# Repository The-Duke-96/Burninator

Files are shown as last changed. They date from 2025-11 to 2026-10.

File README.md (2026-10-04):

# Burninator v3.0 💪🐉🔥
This toolhead is yet another 4010 toolhead, heavily inspired by the [Dragonburner](https://github.com/chirpy2605/voron/tree/main/V0/Dragon_Burner) and the [A4T](https://github.com/Armchair-Heavy-Industries/A4T/tree/main), all props to them.  
Thanks to Reddit user pd1zzle for suggesting the toolhead name, I really took a liking to it.  
Thanks to Reddit user linuxgangster for suggesting, testing, and providing feedback for the MadMax toolchanger adaptation.  
Thanks to Reddit user Such_File_1825 for testing and providing feedback on the MGN7H carriage for V0
And thanks to anyone, who gave any suggestions, gave feedback, was sharing or contributing usermods.
 
<p>
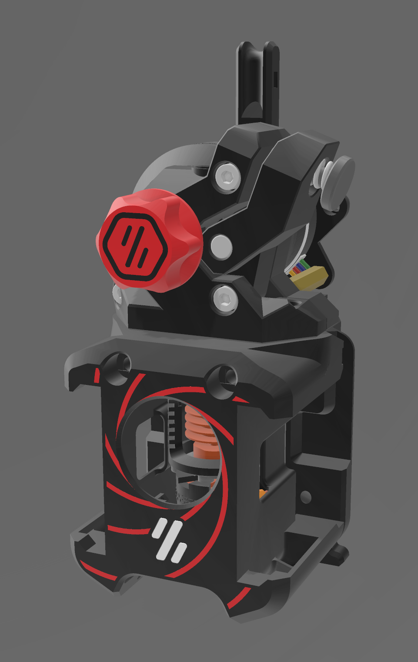
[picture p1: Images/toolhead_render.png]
 
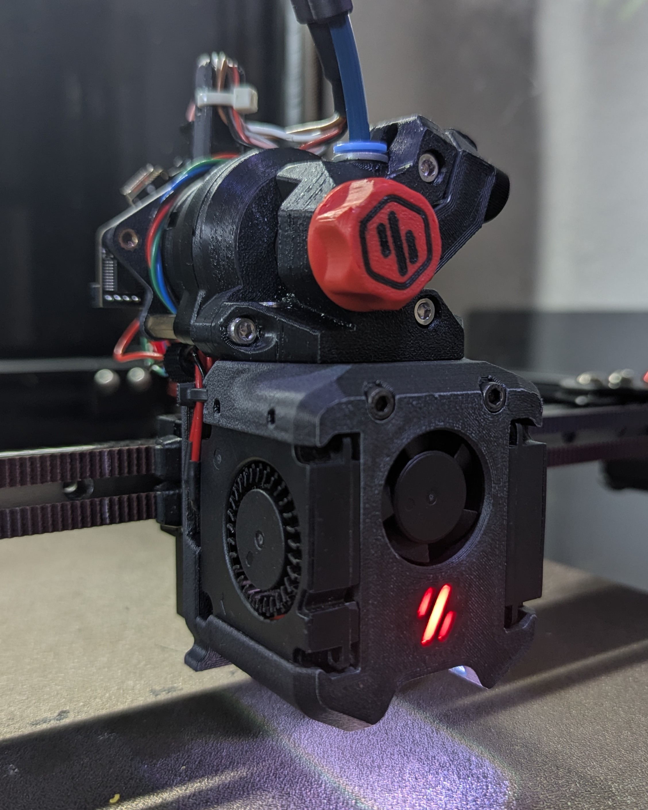
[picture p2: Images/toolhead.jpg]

</p>
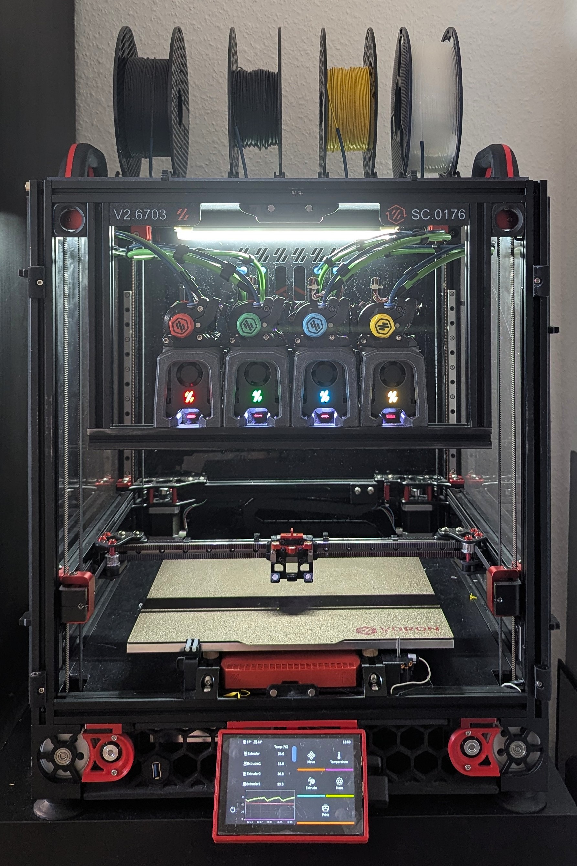
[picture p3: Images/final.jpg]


## But why?  
I created this toolhead because I wasn’t quite happy with the current toolhead options for my Stealthchanger.
After some testing, I decided to create my own toolhead to suit my use case and my printer.
I took features from the Dragonburner and the A4T and put them together, resulting in the Burninator.

## Features:
- Very small and compact, yet fits UHF hotends
- Monolithic cowl design
- Easy assembly and disassembly
- Stronger, 1.2 mm thick walls
- CFM optimized cooling and A4T's backflow inhibitors
- MGN12H, MGN9H, and MGN7H carriages compatible with up to 10 mm belts
- MGN12H and MGN9H carriages also compatible with the [Monolith_Gantry](https://github.com/Monolith3D/Monolith_Gantry) mod, as well as beacon,cartographer and klicky probe
- MGN12H also compatible with Tridex (6mm belts)
- StealthChanger ready
- MadMax ready

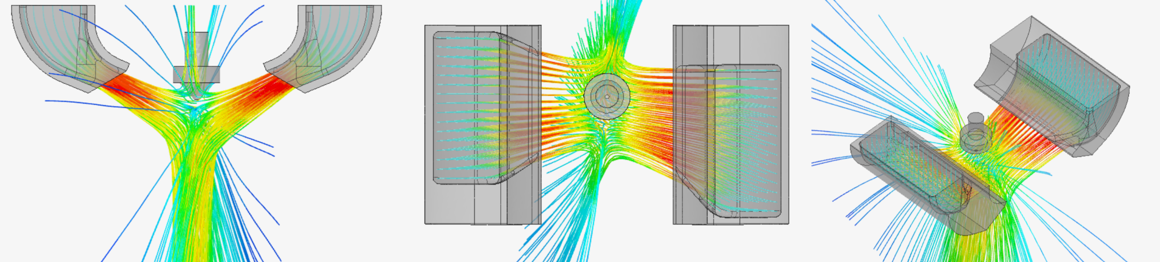
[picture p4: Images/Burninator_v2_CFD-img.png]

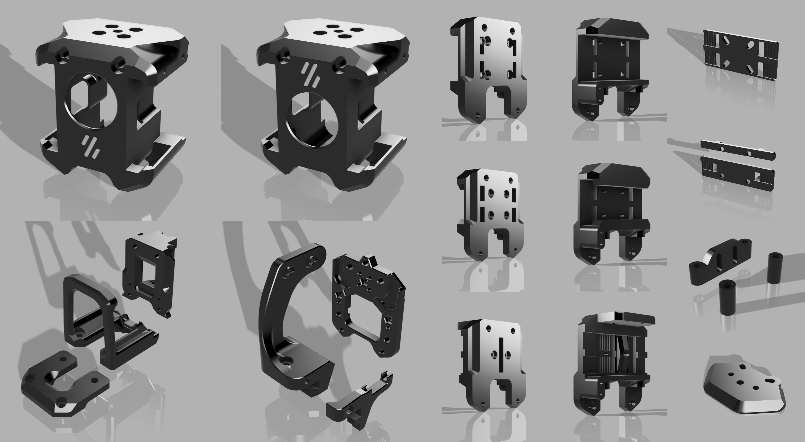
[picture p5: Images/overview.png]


## Compatibility:

**Hotends:** 
- Any top-mounted, Phaetus-style hotend
- SF: Dragon, NextG, TZ, etc.
- UHF: Dragon UHF, NextG UHF, Rapido HF, Dragon ACE (with spacer)
- Rapido UHF
- CHC-XL (+MZE)

**Extruders:**
- Orbiter / Galileo 2
- Sherpa Mini
- Sherpa Micro
- ECAS / Bowden
- LGX & LGX Lite (using the `LGX_adapter`)
- Or similar

**Note:**
- Using the custom parameters in Autodesk Fusion 360, you can adapt the design to almost any Phaetus-style, top-mounted hotend and extruder.

## What is planned?
Waiting for user feedback, opened issues, and suggestions or recommendations. I might also test out some ideas for potential future versions. Other than that, not much for now.  
Of course, CAD files are available for you to modify to your needs, and if you want, you can contribute is as a [Usermod](https://github.com/The-Duke-96/Burninator/tree/main/Usermods)
- looking into adding grove mount compatibility.

## How to Assemble?
Here's the [BOM](https://github.com/The-Duke-96/Burninator/blob/main/BOM.md).      
Here's a handy-dandy [Assembly manual](https://github.com/The-Duke-96/Burninator/blob/main/Assembly%20Manual.md).   

## Disclaimer:
- **Z-Axis Clearance:** If you use printed Z-joints, the toolhead's compact size might cause the Z-rail carriage to hit the frame before the nozzle touches the bed. Workaround: Add taller spacers under the print bed or use shorter Z-joints.  
- **StealthChanger Door Buffer:** If using a door buffer, the `DraftShift_dock_adapter` is required, otherwise the shuttle cannot reach the toolhead.  
- **Sensor Mounts:** Ensure the `beacon/cartographer_spacer`, or `klicky_mount` is scaled in the Z-axis to fit your specific setup.  
- **Beta Files:** Some files are untested by me. If anything does not fit or work as expected, please open an issue or let me know.
- **Macro Adjustments:** Stock StealthChanger pickup and dropoff paths work, but you might need slight adjustments for the nozzle to properly scrub the wiper.  

```
params_dropoff_path: [{'y': 25, 'z':6.5}, {'y': 5, 'z':6.5} , {'y':0, 'z':6.5, 'f':0.5}, {'y':0, 'z':0, 'f':0.5}, {'y':0, 'z':-10}]
params_pickup_path: [{'y':0, 'z':-10}, {'y':0, 'z':0, 'f':0.5, 'verify':1}, {'y':0, 'z':6.5, 'f':0.5}, {'y': 25, 'z':6.5}]
```

## Support:
<a href="https://ko-fi.com/theduke96">
  
</a>

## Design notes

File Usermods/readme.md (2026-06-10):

## Usermods

If you modified the Burninator and want to share it with others, feel free to contribute a user mod.

- Fork the repository.  
- Create a folder in `Burninator/Usermods` with a descriptive name.  
- Add your files and optionally include a README with instructions or further information.  
- Create a pull request.  

**Note:**  
The following usermods:  
- Tridex carriage (just a test)  
- StealthChanger dock for Rapido-UHF  
- StealthChanger dock for CHC-XL  
- MGN12H_invertable_belt_fixture for 9 mm belts  
- Cowl for CHC-XL + MZE  
have been removed from the usermods because they were provided by me and are now integrated into Burninator v3.0

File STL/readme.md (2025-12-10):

# STL Files

- v1 is the old / first uploaded version.
- v2 is the new and current version, featuring optimized ducts for improved part-cooling performance.  
**Note:** v1 and v2 are not fully compatible, due to changes in the duct geometry and screw-hole locations, the dock, its cosmetic, the backplate, and the carriages all had to be adjusted accordingly.
- All printed parts are already oriented correctly for printing.
- Required print supports are built in.
- Cosmetics and their corresponding parts must be printed together, just align them and decide if and how you want to color them.  
**Note:** Aligning the cosmetic to the cowl, either eyeball it or use the following reference offsets:  
UHF cowl on X0/Y0, cosmetic X-1,75/Y0.35  
SF cowl on X0/Y0, cosmetic X0/Y-2.03

- For the LED diffuser, it's recommended to print it in white or clear filament. You can also leave out the logo LED and print it in any color you want.

---

# Assembly Manual

- Start by installing the heat inserts: two in the bottom rear, two on top of the cowl, two at the top of either the StealthChanger backplate or the MGN12H / MGN7H carriage, two in the back of the EBB mount, one in the bottom of the dock, and two M5 inserts in the dock adapter.

<p>
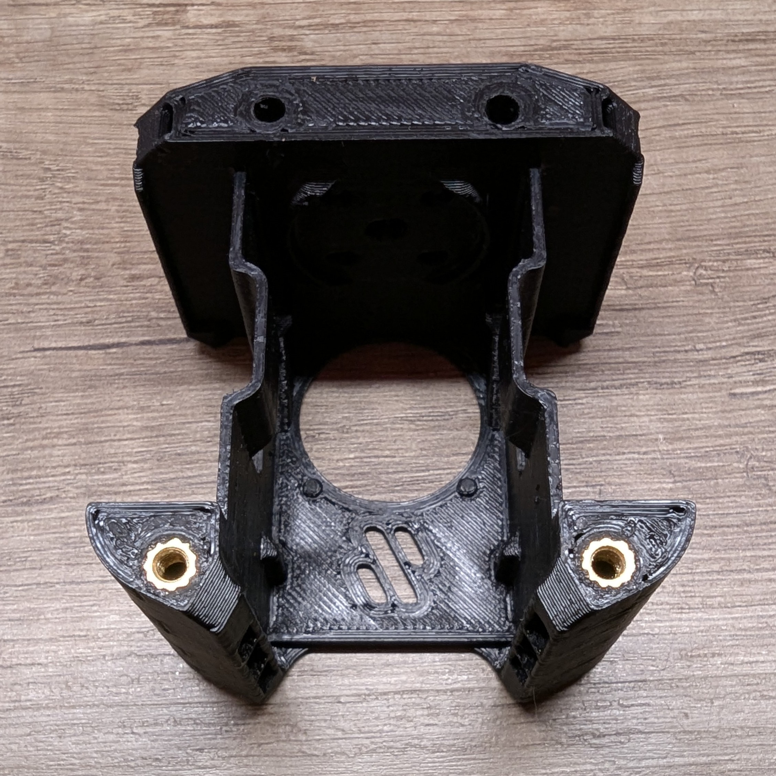
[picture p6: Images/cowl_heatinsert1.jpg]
 
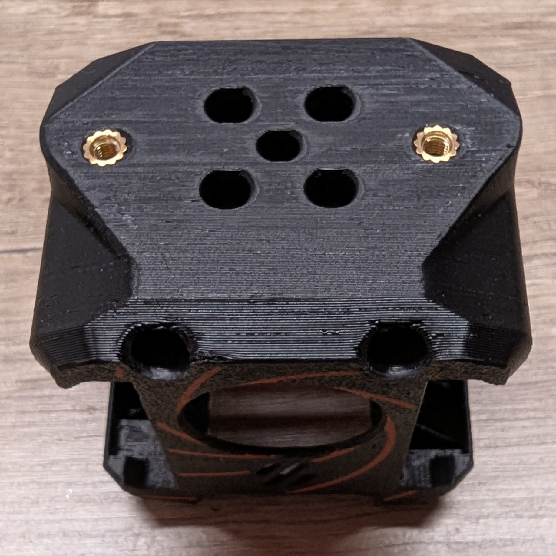
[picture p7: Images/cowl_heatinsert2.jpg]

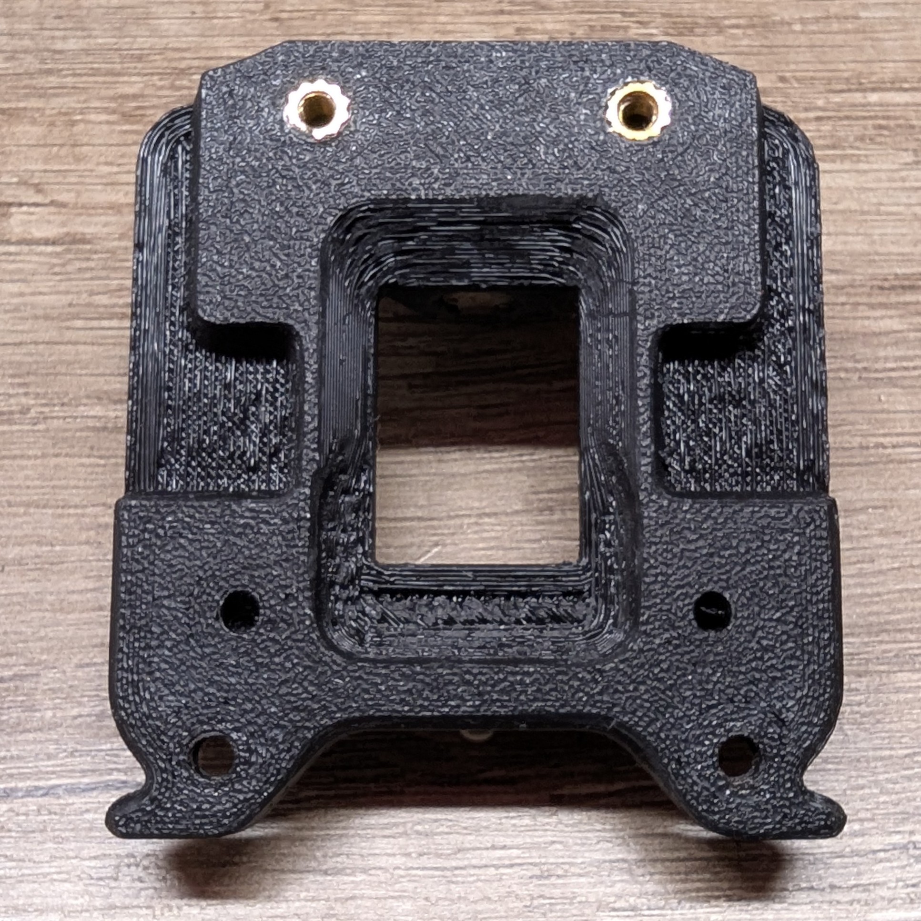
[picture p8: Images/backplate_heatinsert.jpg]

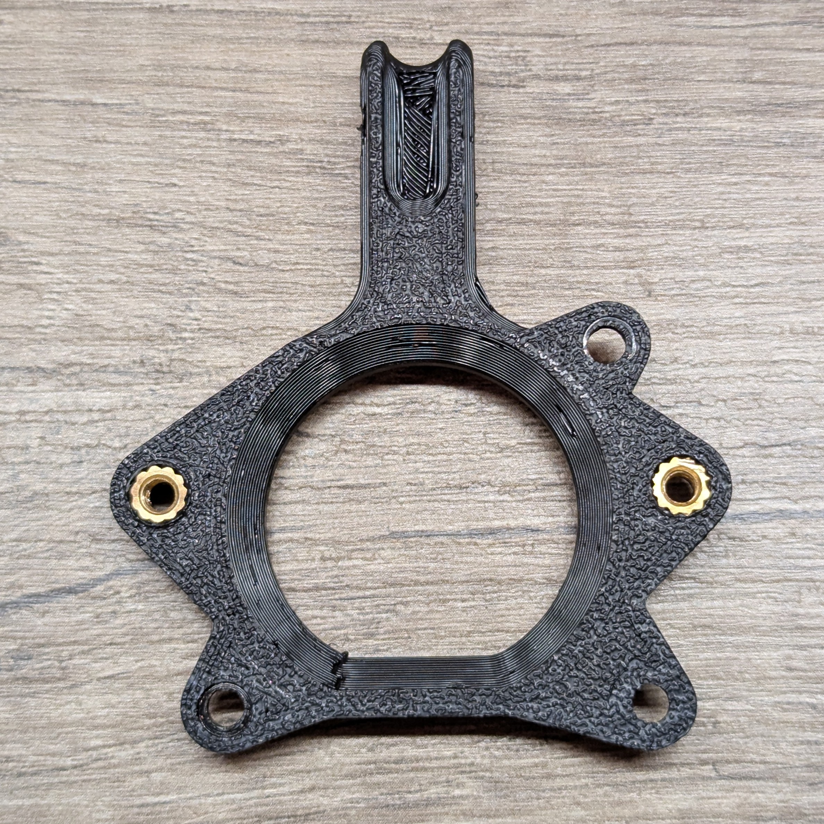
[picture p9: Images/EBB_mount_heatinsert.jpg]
 
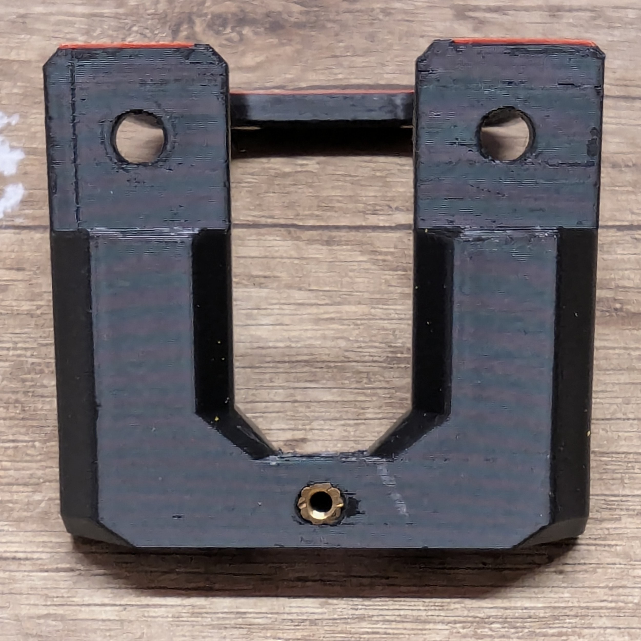
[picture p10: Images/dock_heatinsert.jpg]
 
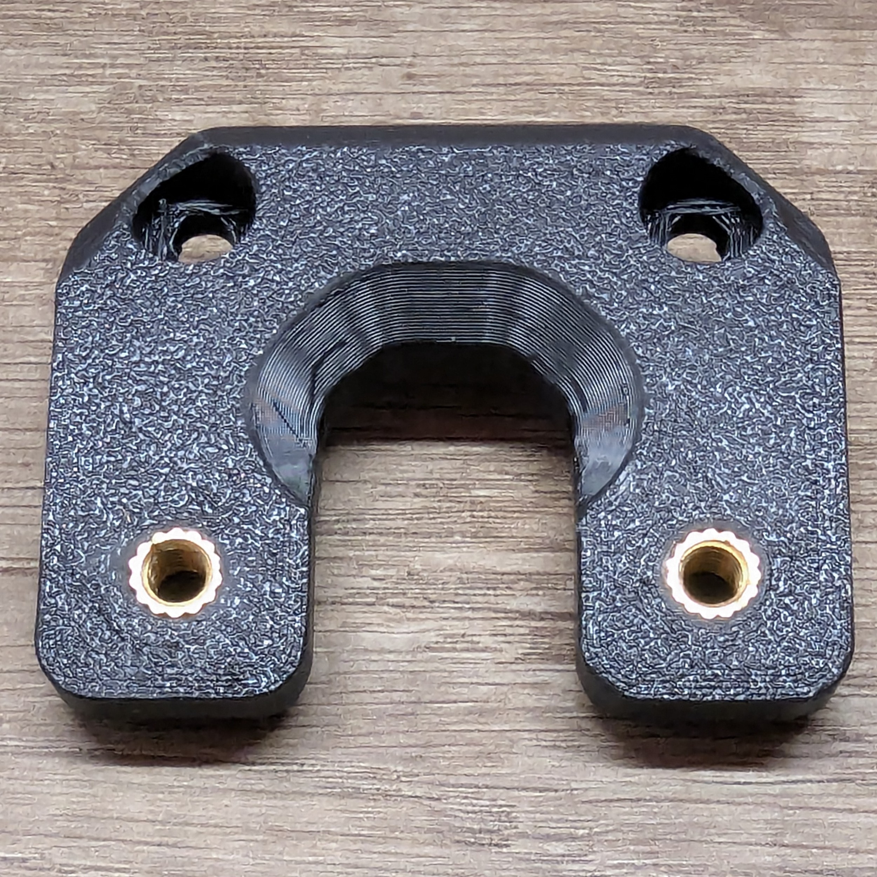
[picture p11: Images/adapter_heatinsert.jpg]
 
</p>

- Insert the 2510 fan from the back and slide it upward, wedging it into place. The two small nubs should fit into the bottom holes of the fan, securing it further. This works the same way as on the Dragonburner.
- Insert the LED diffuser into the Voron logo cutout.

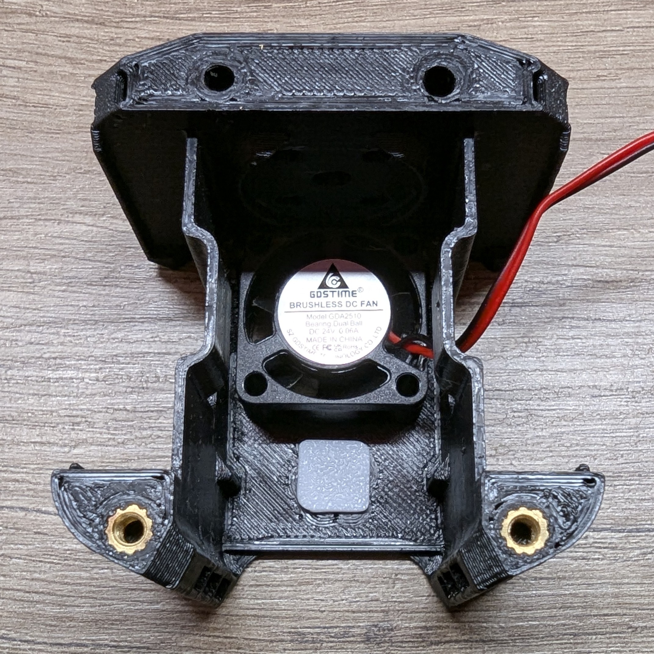
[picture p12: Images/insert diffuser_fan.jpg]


- Continue with soldering the LEDs. You'll need six pieces of 20mm wire and three pieces of 170mm wire.
- Solder the first three short wires to the OUT pads of the first LED.
- Solder the second LED, facing the opposite direction of the first.
- Solder the last three short wires to the second LED, facing the same direction as the first set.
- Solder the third LED so that it faces the same direction as the first LED and opposite the second.
- Solder the 170mm wire to the IN pads and crimp on the connector.  
  **Note:** Make sure the wires are soldered in the correct orientation as shown in the picture.
  
<p>
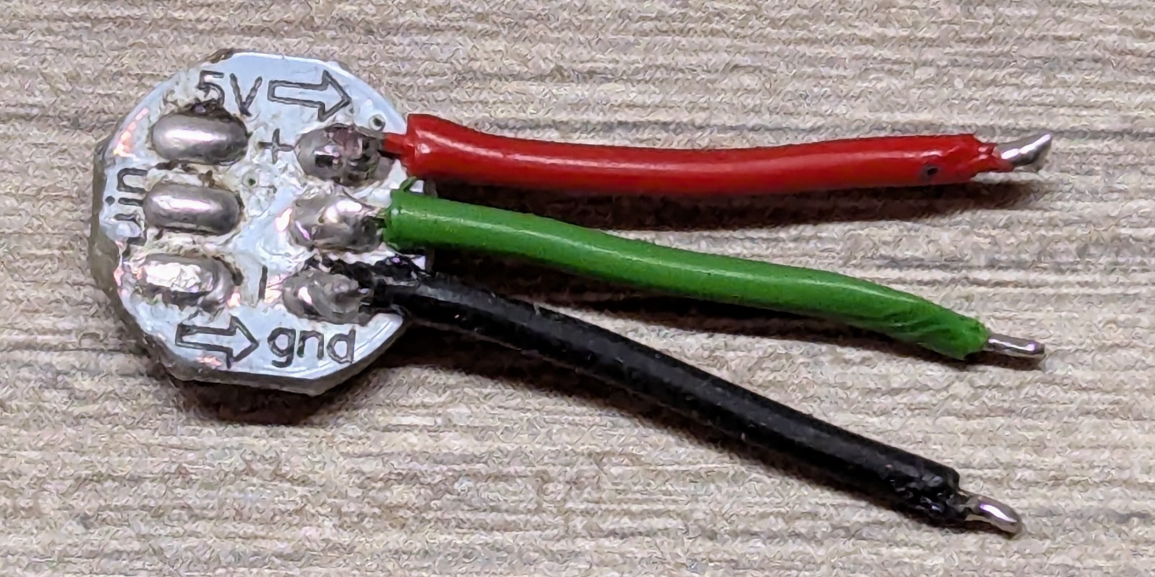
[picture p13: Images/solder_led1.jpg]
   
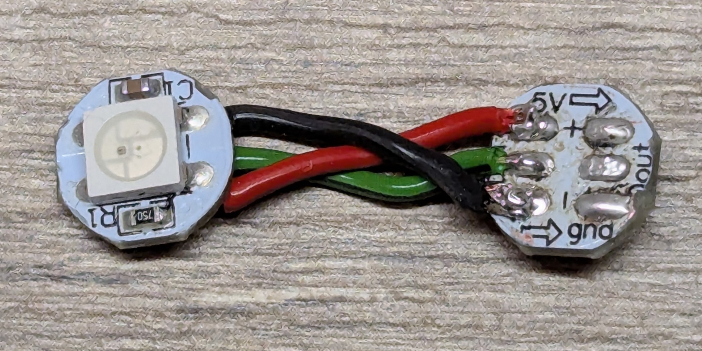
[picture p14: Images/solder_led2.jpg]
   
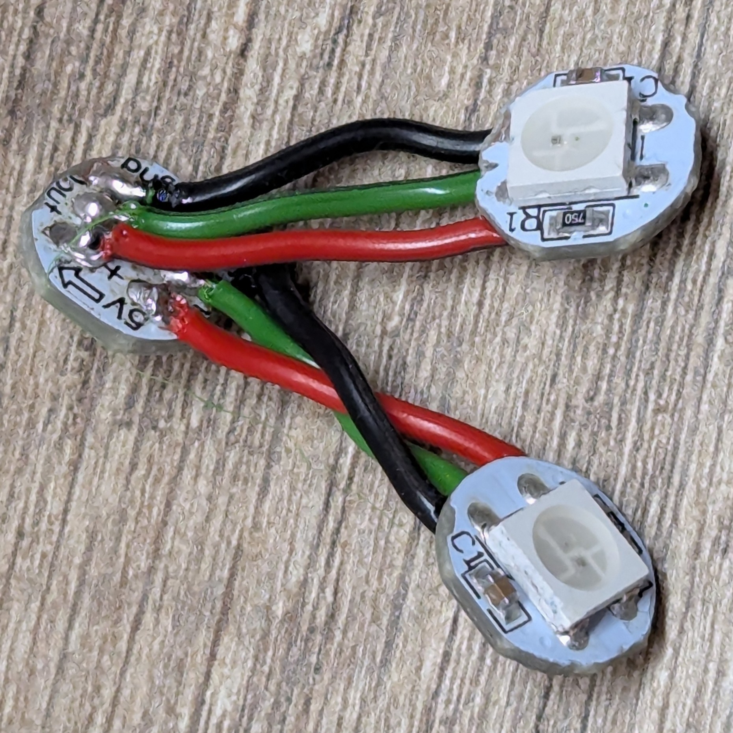
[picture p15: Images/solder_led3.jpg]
  
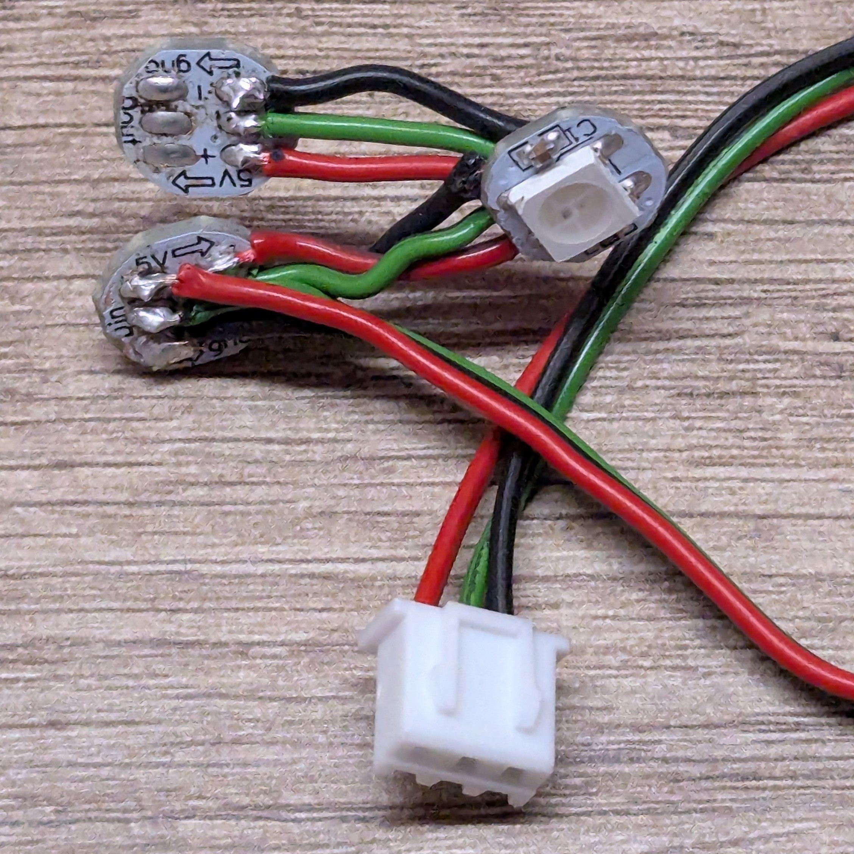
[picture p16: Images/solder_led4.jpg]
 
</p>

- Insert the second LED into the LED carrier first, then the remaining two, it’s easier that way.
- Insert the LED carrier from the back, placing the bottom edge into the cowl ledge. Tilt it, then press it firmly into place. Ensure the diffuser is seated in the front groove of the LED carrier.

<p>
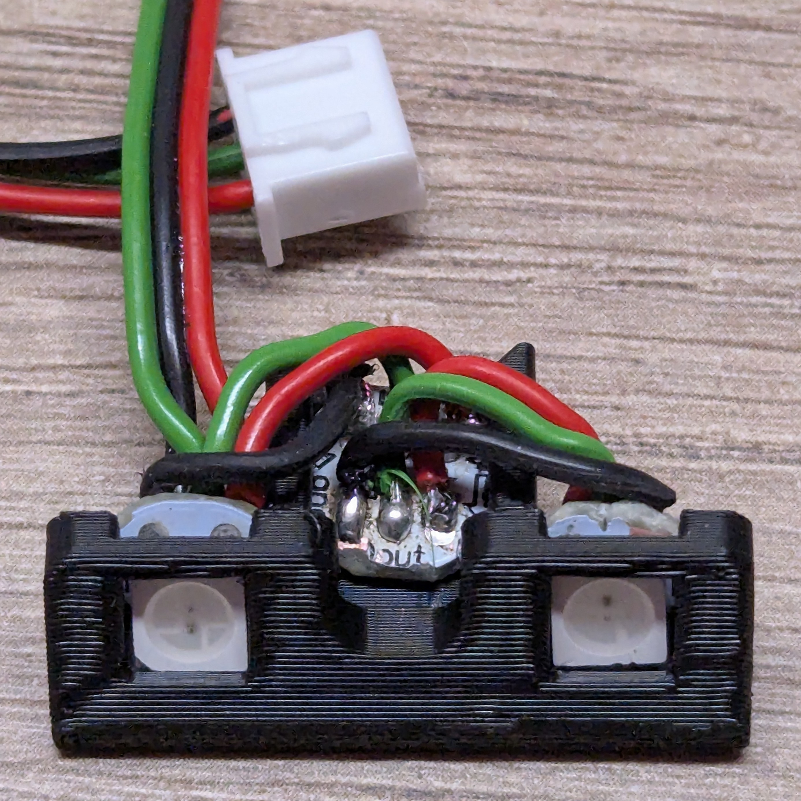
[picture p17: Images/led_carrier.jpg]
   
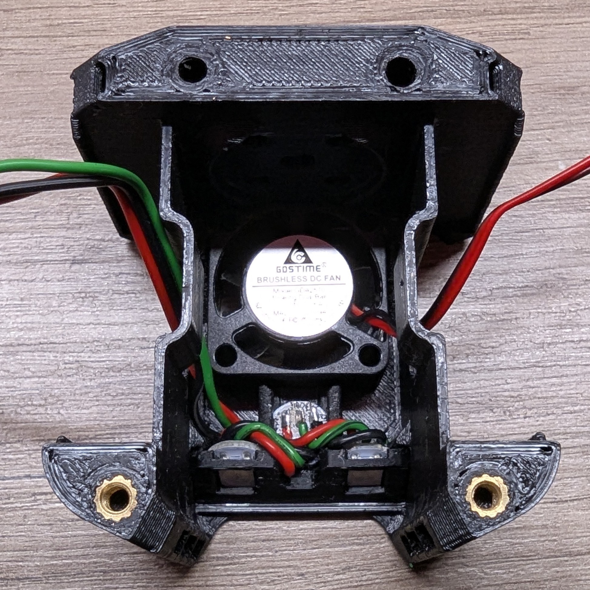
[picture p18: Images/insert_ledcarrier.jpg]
   
</p>

- For the 4010 fans: remove the front cover and glue in A4T’s Backflow Inhibitor (optional but recommended).  
  After the glue has dried, put the cover pack on.
- One of the fans needs its wires bent toward the back. You may also resolder the wires.
- Slide the fans into the sides of the cowl, same as on the Dragonburner.

<p>
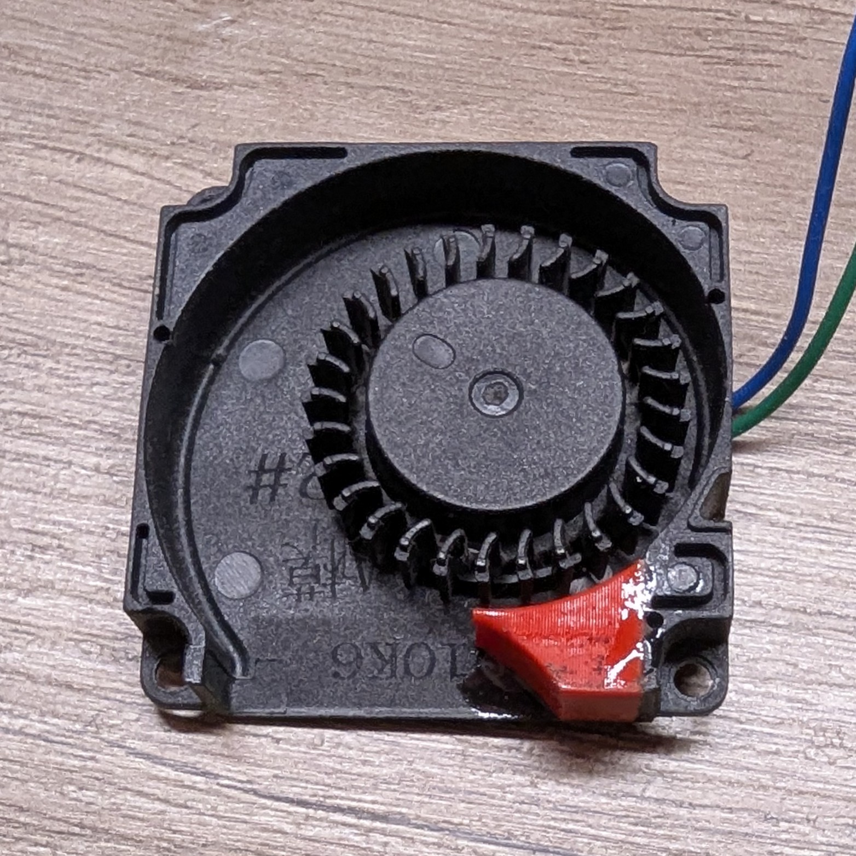
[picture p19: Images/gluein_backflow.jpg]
   
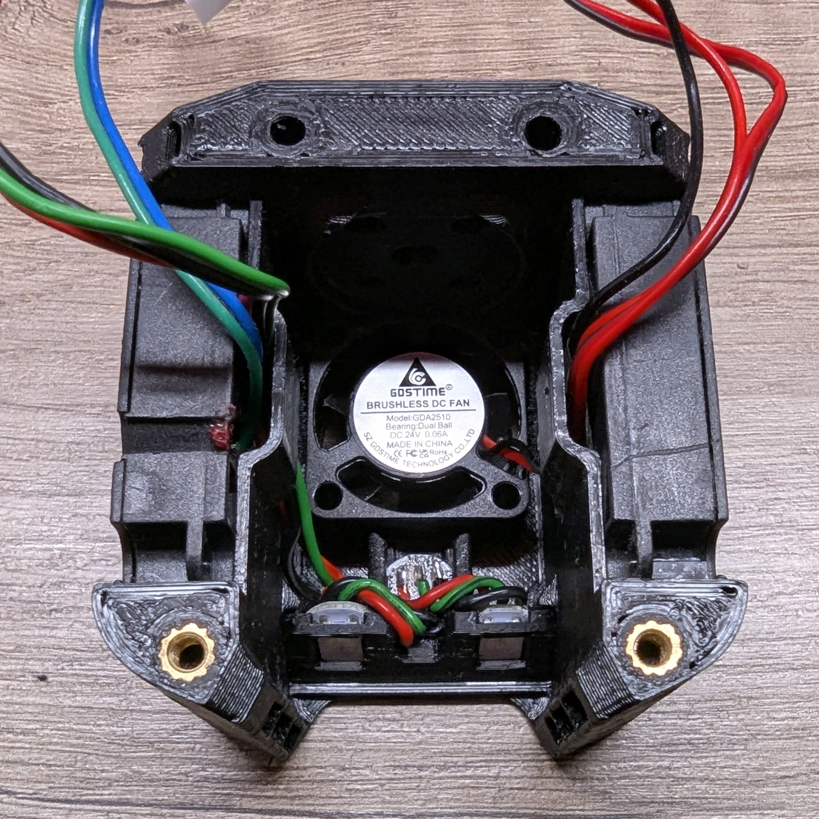
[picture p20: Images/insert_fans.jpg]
   
</p>

- Install the hotend. In my case, a Dropeffect NextG Fiber UHF is used. Ensure it's rotated correctly so the cables point toward the back corner.
- Route the thermistor wire with the cable sleeve to the opposite side, as it will not fit through the cowl and backplate cutouts. Route the heater wires on the other side, bending them so they will fit cleanly.

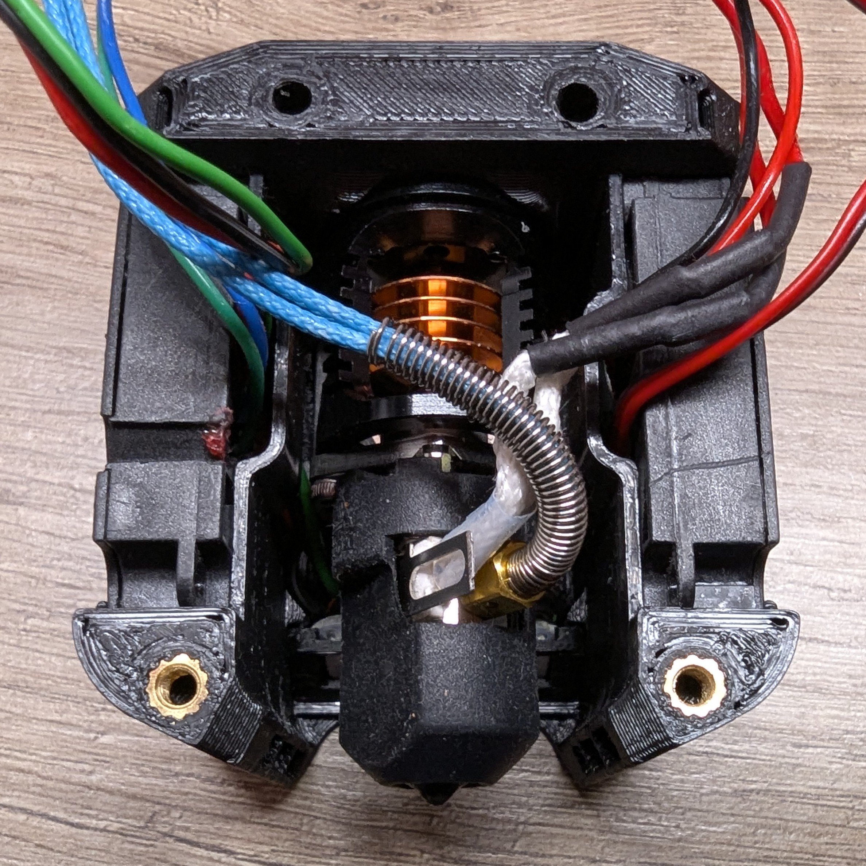
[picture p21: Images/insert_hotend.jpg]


- Place the backplate, wiggle the cables into position, and ensure the metal hose sits inside the backplate groove underneath the center hole. Screw it down.
- Install either M3x40 SHCS screws with a 3 mm spacer, or M3x35 SHCS screws without the spacer and place a 6×3 mm magnet on top.
- Route cables into the grooves and secure them with zip-ties.
- If using the StealthChanger backplate, install the OptoTap PCB.

<p>
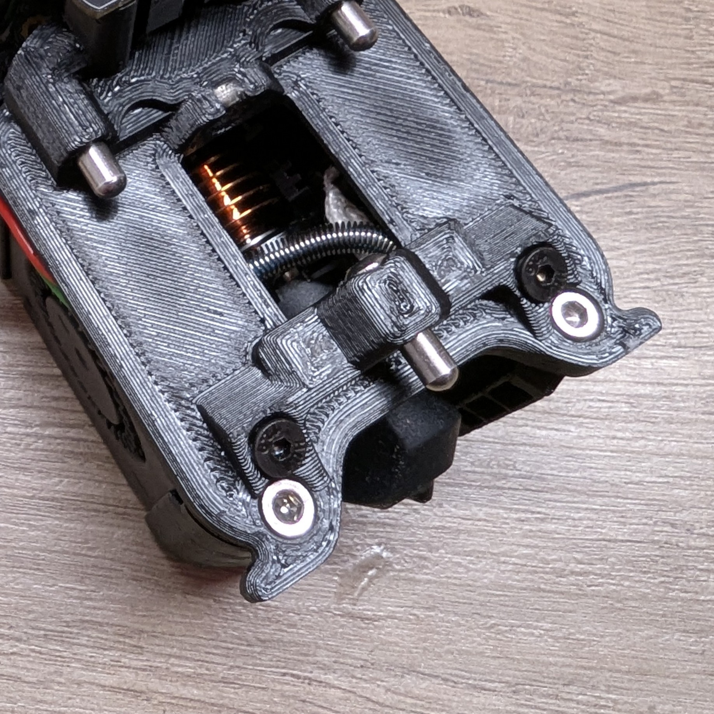
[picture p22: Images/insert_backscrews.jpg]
   
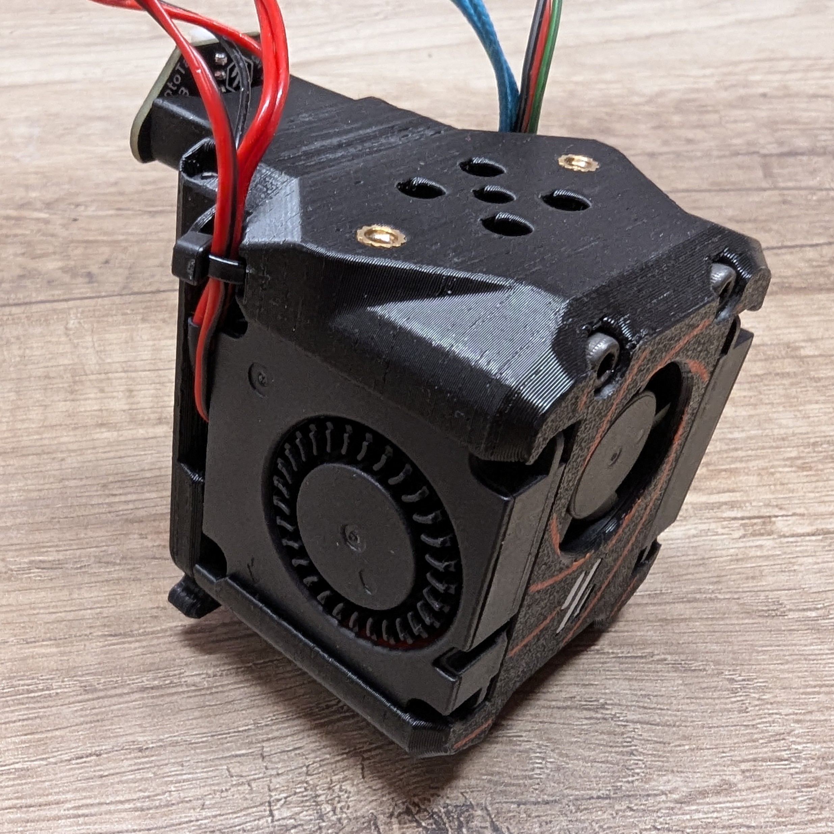
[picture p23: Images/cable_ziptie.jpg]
   
</p>

- Install a 22 mm PTFE tube and mount your extruder. In this example, the Galileo 2 WristWatch is used, followed by the toolhead PCB.
- In this setup, the EBB36_G2WW_Mount is required due to interference from the OptoTap.
- The toolhead is now complete.

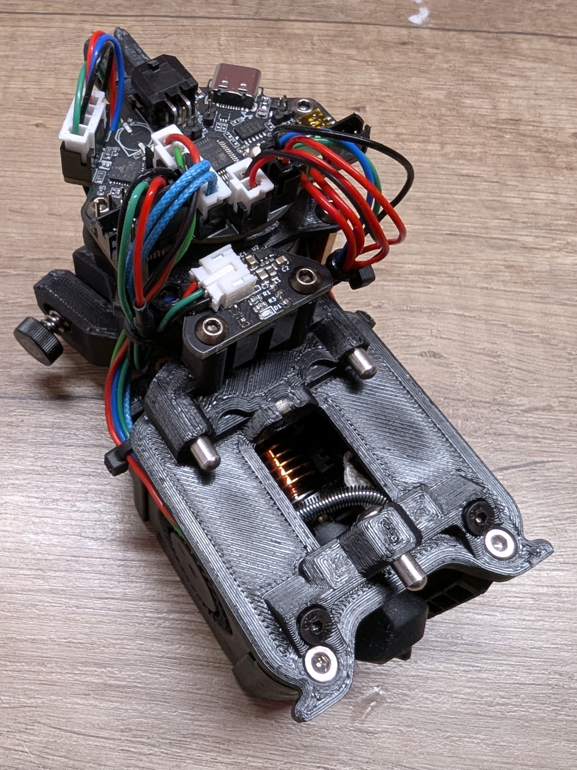
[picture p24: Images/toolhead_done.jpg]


---

# Cowl SF Assembly

- Assembling the SF cowl is only a little bit different from the UHF cowl.
- For soldering the LEDs, you need wires in the following lengths: 3 × 47 mm, 3 × 30 mm, and 3 × 170 mm.
- Start with the last LED and solder the 47 mm wires to the IN.
- Now solder the second LED, and then the first LED, using the 30 mm wires.
- Finally, solder the 170 mm wires and crimp on the connector.  
  **Note:** Make sure the wires are soldered in the correct orientation as shown in the picture.
- After that, place them into the LED carrier.

<p>
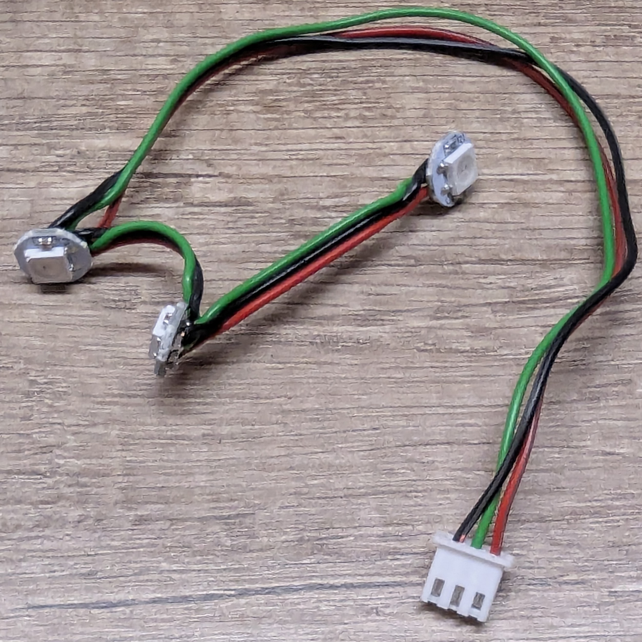
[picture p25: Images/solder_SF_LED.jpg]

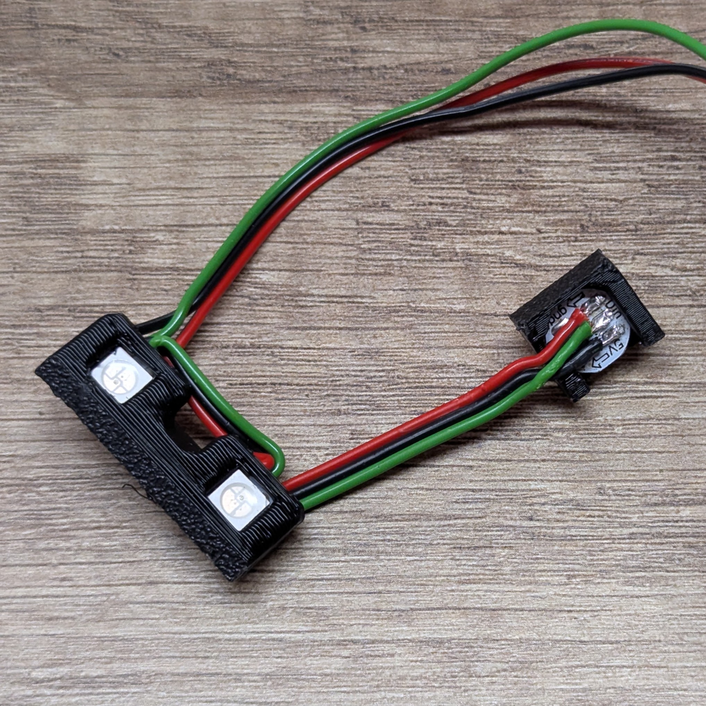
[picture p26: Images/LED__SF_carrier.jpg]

</p>

- Moving on to the cowl: first insert the LED diffuser and the top LED carrier. The cable should exit sideways into the cable channel.  
**Note:** Inside the cable channel are two little support ribs, as printing support. Just cut them away, 

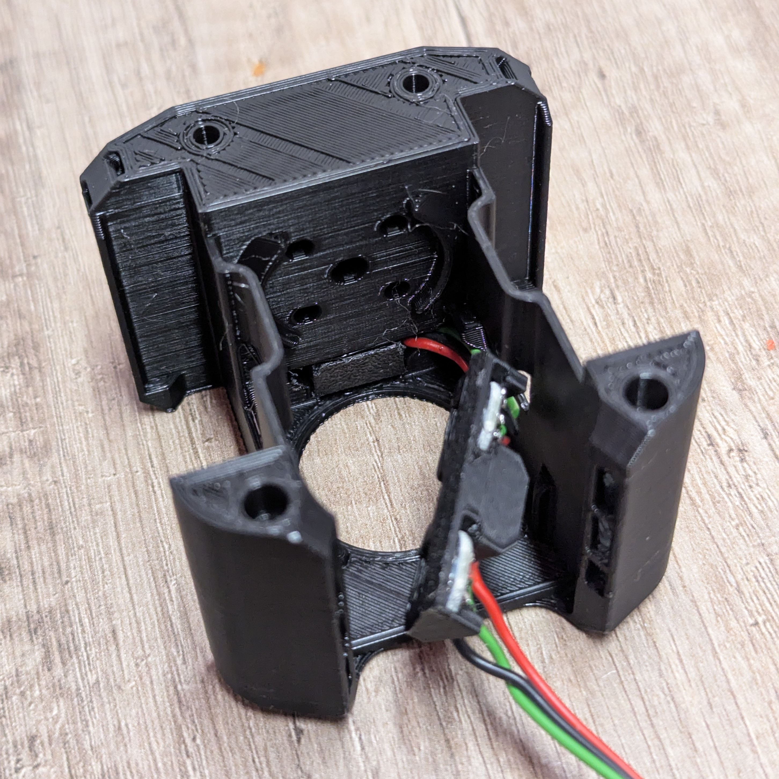
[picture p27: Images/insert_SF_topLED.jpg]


- Then tuck the cable into the corner and run it down along the wall. Push the larger LED carrier aside and insert the 2510 fan.
- After that, push the larger LED carrier into place.  
  **Note:** Due to the tight space, routing the cable and seating everything can be a bit tricky. The better the soldering job and the thinner the wires, the easier it gets.

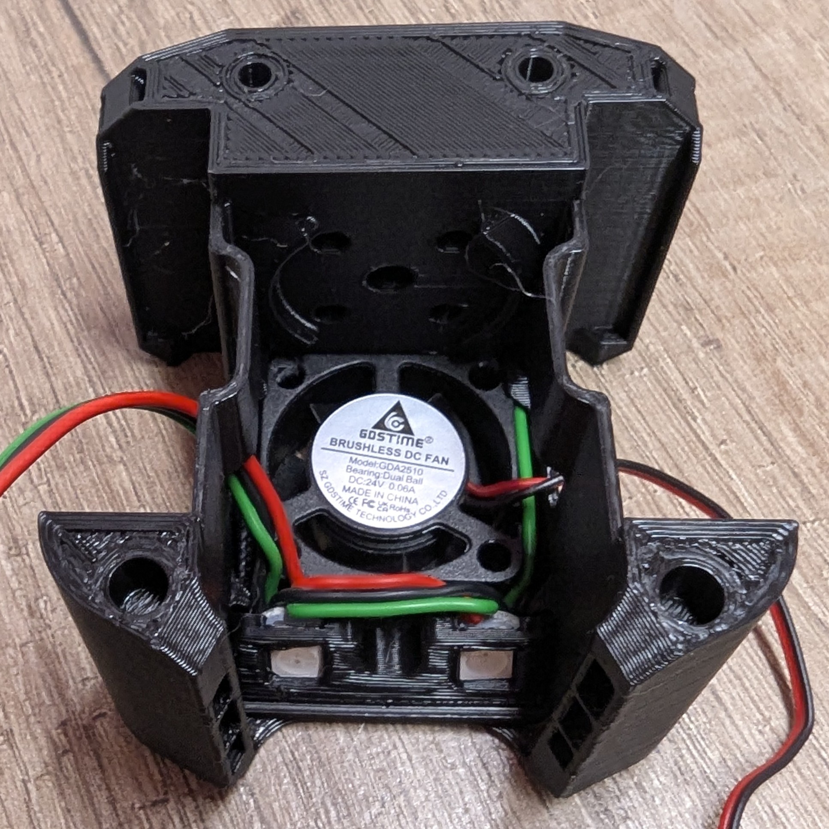
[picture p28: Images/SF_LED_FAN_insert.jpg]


---

# Dock Assembly

- Insert the 31 mm spring steel blocker into the rear slit and secure it with an M3x5 screw.
- Take a 23 mm PTFE tube for the wiper, bend it in the middle, wedge it into the back holder, then press down to straighten it out.
- Press the magnets into the top.
- Mount the dock onto the crossbar, optionally using the adapter.

<p>
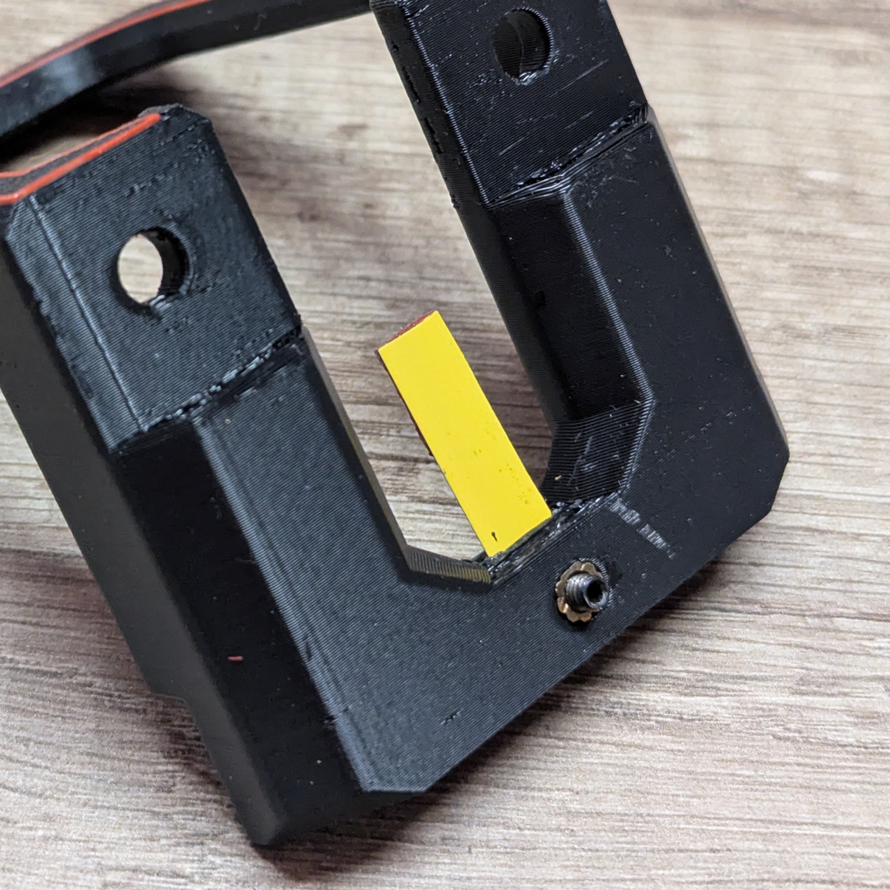
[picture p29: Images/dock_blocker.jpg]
   
   
</p>

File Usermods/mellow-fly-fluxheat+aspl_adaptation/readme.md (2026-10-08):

# Mellow Fly Fluxheat with ASPL level sensor adaptation
UHF cowl and MGN12/9/7H Backplate adjusted for the Mellow Fly Fluxheat with ASPL level sensor, using the CAD parameters as well as a shim to mount the aspl pcb between the EBB36 mount and EBB36 pcb.
As by userrequest, I have added it here as a usermod.

## fly-aspl_adapter.stl


**note:**
- Put a M3 heat insert into the center hole.
- A litte bit of support is needed.
- don't  forget the appropriate belt clampage parts 
- Using the fly-aspl_adapter, will extend the toolhead into the back by 8mm! Connectors on the side should be still accessable.  

## fly-aspl_adapter_v2.stl


**note:**
- Put a M3 heat insert into the center hole.
- no support needed
- put this behind the EBB36_mount
- use sufficiently long standoffs

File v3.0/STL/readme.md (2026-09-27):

# STL Files

- Objects are not oriented correctly and do not have built-in support structures. Keep this in mind when slicing, using manuall support just on the critical faces is recommended.
- Print the `LED_diffuser`, and optionally the `LED_carriage`, in white for better light distribution.
- Scale `klicky_mount` and `beacon_cartographer_spacer` in Z to your needs.
- Print settings: Follow the Voron Design advice [here](https://docs.vorondesign.com/sourcing.html)

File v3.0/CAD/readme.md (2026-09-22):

# CAD Files

- Use these files if you wish to modify something.  
- Keep in mind that the fan duct must blow air to the correct area: the tip of the hotend nozzle should sit about 2 mm beneath the lowest part of the cowl.  
- `backplate_base`, `SC_shuttle_base` and `MGNxH_carriage` are base bodies you can use to build upon.
- Extruder mounting holes and the ECAS adapter are present as a negative bodies that needs to be cut out.  
- I made use of custom parameters you can use to adapt the toolhead to almost any hotend:  
  - `hotend_length`: Lengthens the cowl to your hotend size.
  - `hotend_screwhole_radius`: Adjusts the hotend mounting holes.
  - `DS_adapter_length`: Shortens or lengthens the adapter to fit your existing DraftShift docks.
  - `extruder_screwholes_left`: Adjusts the center distance for the left extruder mounting hole.
  - `extruder_screwholes_right`: Adjusts the center distance for the right extruder mounting hole.
  - `heat_insert_diameter`: Adjusting the hole size for the M3 heated inserts.
- I also provided a convenient Python export script that I use. It changes the parameters, makes the cuts, and exports all the files.  

**Note:** 
The Python script was written with the help of AI. 
I'm way too stupid to do it myself, so I claim no credit for it. 
All credit goes to those, which training data were used.

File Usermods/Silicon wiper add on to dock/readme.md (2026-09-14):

Direct replacement of PTFE tubing wiper in favor of a silicone wiper. 

This is designed to be a bit tight of a fit into the existing PTFE slot. No modifications to the dock itself but you have have to snap them into place. The wiper used [is these that are common on the A1 printers](https://a.co/d/09I6NoFP) so they are available from all over the place. They are trimmed down to about 4 rows and slide into place from one side. The ones i had have some glue on the bottom with a peel off strip to expose it. I would imagine most do but a drop of glue would work too if needed. 

The print should be with the Nozzle wiper portion facing up. Some support of whatever flavor you like on the bottom, it's a super fast print so it's easy enough to do some testing with what works for your setup.

When installing put the short overhang side out toward the shuttle and the 45 degree slash in toward the dock body. If you insert backwards the pin slots on the dock will catch when grabbing/dropping off and make less than ideal noises. 

<p align="center">
  Dock wiper
</p>

<p align="center">
  Front View
  Back View

The original docking params may need to be adjusted for the wiper similar to the adjustments made for the PTFE tube version in the main repo. 

The magic values to get a little wipe on the way in and on the way out is the First 2 on Z on drop off and the last Z on pickup. If those number are different you get a little bit of a ramp, i have them at the same level right now so it wipes across the wiper just enough to pass through but now so low as to try to pull the wiper from the cradle. It's certain a little balance but it's not hard to find. 

I changed them both from 4 to 2 (based on the original Easy-tool-changer repo numbers) so it wipes directly across the silicone pad instead of coming up high just across the top of the wiper. 

```
params_dropoff_path: [{'y':9.5 ,'z':2}, {'y':9.5, 'z':2}, {'y':5.5, 'z':0}, {'z':0, 'y':0, 'f':0.5}, {'z':-10, 'y':0}, {'z':-10, 'y':16}]
params_pickup_path: [{'z':-10, 'y':16}, {'z':-10, 'y':0}, {'z':0, 'y':0, 'f':0.5, 'verify':1}, {'y':5.5, 'z':0}, {'y':9.5, 'z':2}, {'y':9.5 ,'z':2}]
```

In order to tune this the Dock_Tuner Macros work great to come at them slowly and test your height requirements with minimal carnage.

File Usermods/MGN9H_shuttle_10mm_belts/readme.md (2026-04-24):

# Shuttle for MGN9H shuttle with 10mm belts
This is a modified StealthChanger shuttle for the MGN9H and 10 mm belts, it uses the shuttle keeper modified as well for MGN9H and 10 mm belts.
Use this and proceed as shown in the StealthChanger documentation.

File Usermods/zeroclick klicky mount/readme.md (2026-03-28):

# Zeroclick Klicky Mount
A simple mod of the zeroclick probe to mount it like the klicky probe

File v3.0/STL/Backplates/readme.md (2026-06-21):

# Backplates
**note:**
Use the _alt (alternative) belt_clamp_plates, if you have trouble with the belts. Those are thicker and allows the belt be loop and clamp from both sides, but it also adds 1.4mm in Y.

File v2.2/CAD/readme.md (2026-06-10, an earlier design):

# CAD .step file

- Use these files if you wish to modify something. 
- “Burninator_RAW.step” offers a clean base version of the Burninator, with no cosmetics, no spiral pattern, no extruder mounts, and no front LED logo, so you can use it as a foundation to build on.
- Keep in mind that the fan duct must blow air to the correct area: the tip of the hotend nozzle should sit about 1.5 mm beneath the lowest part of the cowl.
- The CAD files do not include the subtraction for the MadMax screw holes on the cowls, in order to keep the file size down.
The component called “cowl_screwhole_extensions” in Burninator, MadMax is exactly what it says. Combine it with any cowl of your choice, do the screw hole subtraction, and you are done.

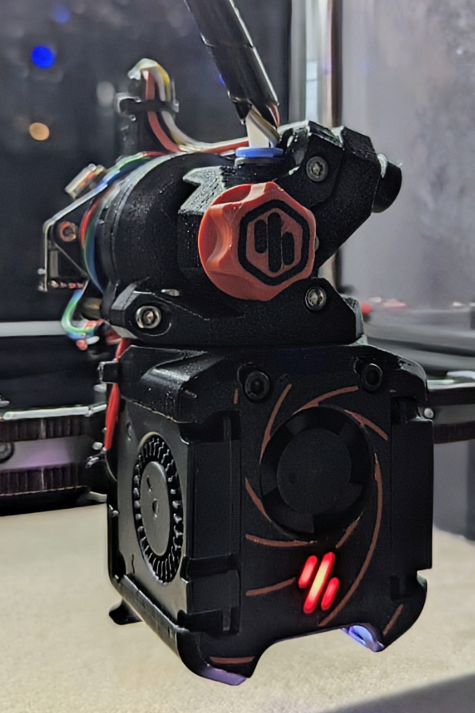
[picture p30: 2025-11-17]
Images/Toolhead.jpg

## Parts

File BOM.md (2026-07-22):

# BOM — Burninator v3.0

## Cowl
- 4x    M3x4mm heat inserts
- 2x    M3x40mm SHCS magnetic 
- 2x    M3x6mm BHCS
- 1x    2510 fan (Delta ASB02505SHA-AY6B or similar high cfm fan recommendet)
- 2x    4010 blower fans
- 1x    LED_diffuser
- 1x    LED_carriage
- 3x    PCB-LEDs (neopixel)
- 1x    hotend
- 4x    M2.5x6-8mm hotend screws (torx BHCS recommended)
- 1x    ptfe tube (short, between hotend and extruder)
- 2x    2,5mm cable zip tie

## MGN12H_ and MGN9H_carriages
- 4x    M3x4mm heat inserts
- 1x    belt_clamp_plate / tridex_clamp_plate(+_opp)  
- 4x    M3x6-8mm SHCS    

## MGN7H_carriage
- 6x    M3x4mm heat inserts
- 1x    belt_clamp_plate / tridex_clamp_plate(+_opp)  
- 4x    M2x4-6mm SHCS   
- 2x    M3x6-8mm SHCS
- 2x    MGN7H_belt_clamp_[2x] 

## klicky_mount and beacon_cartographer_spacer
- 2x M3x(length depending) SHCS

## lgx_adapter
- 4x    SHCS extruder screws
- 2x    M3x6mm SHCS

## SC_backplate
- 2x    M3x4mm heat inserts
- 3x    4x12mm dovel pins
- 5x    M3x8mm BHCS
- 1x    6x3mm N52 magnet
- 2x    M3x6mm FHCS
- 1x    OptoTap PCB sensor

## SC_dock_back
- 1x    M3x4mm heat inserts
- 2x    M3x6-8mm SHCS
- 1x    M3x4mm SHCS (grub screw recommended) 
- 1x    10x28mm spring steel blocker
- 1x    4x19mm ptfe tube

## SC_dock
- 2x    M3x4mm heat inserts
- 2x    6x3mm N52 magnet    
- 2x    M5x10mm BHCS

## SC_adapter
- 2x    M5x8-10mm heat inserts
- 2x    M5x10mm BHCS

## SC_MGN12H_ and _MGN9H_shuttles
- 2x    M3x4mm heat inserts
- 1x    belt_clamp_plate 
- 3x    4x6x6mm bushing
- 3x    6x3mm N52 magnet
- 4x    M3x6-8mm SHCS  

## SC_MGN7H_shuttle
- 2x    M3x4mm heat inserts
- 3x    4x6x6mm bushing
- 3x    6x3mm N52 magnet
- 4x    M2x4-6mm SHCS  
- 2x    M3x6mm SHCS
- 2x    MGN7H_belt_clamp_[2x] 

## MM_backplate
- 4x    M3x4mm heat inserts
- 3x    M3 nut
- 3x    M3x6mm FHCS
- 6x    6x3mm N52 magnet
- 3x    M5x6mm BHCS 
- 1x    M3 ring termianl crimped wire
- 2x    M3x6 BHCS
**note:**
[MadMax BOM](https://github.com/zruncho3d/madmax/blob/main/BOM.md)

## MM_dock
- 1x    M3x4mm heat inserts
- 2x    6x3mm N52 magnet
- 2x    M3x6mm FHCS
- 1x    M5x10mm BHCS
- 1x    25x6mm spring steel blocker

## MM_ptfe
- 1x    M3x6mm SHCS
- 1x    4x25mm ptfe tube

## EBB36_mount
- 4x    M3x6-8mm BHCS
- 2x    M3x21mm standoff

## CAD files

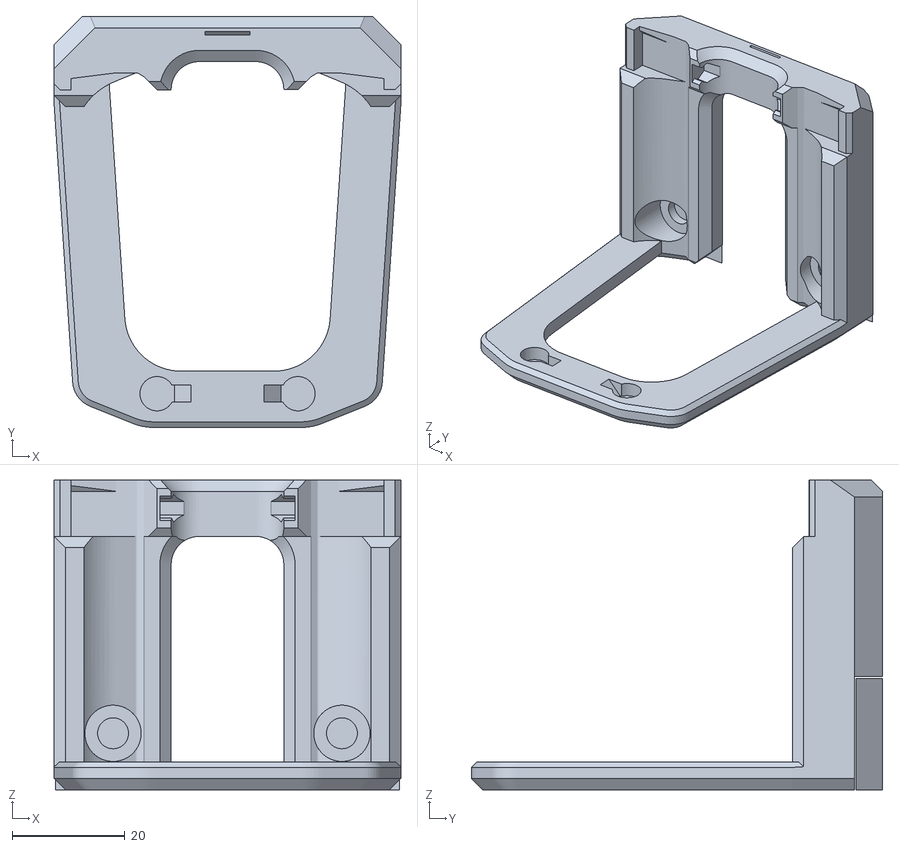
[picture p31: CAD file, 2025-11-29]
STL/v2/dock.stl
61.5 x 72.9 x 55.0

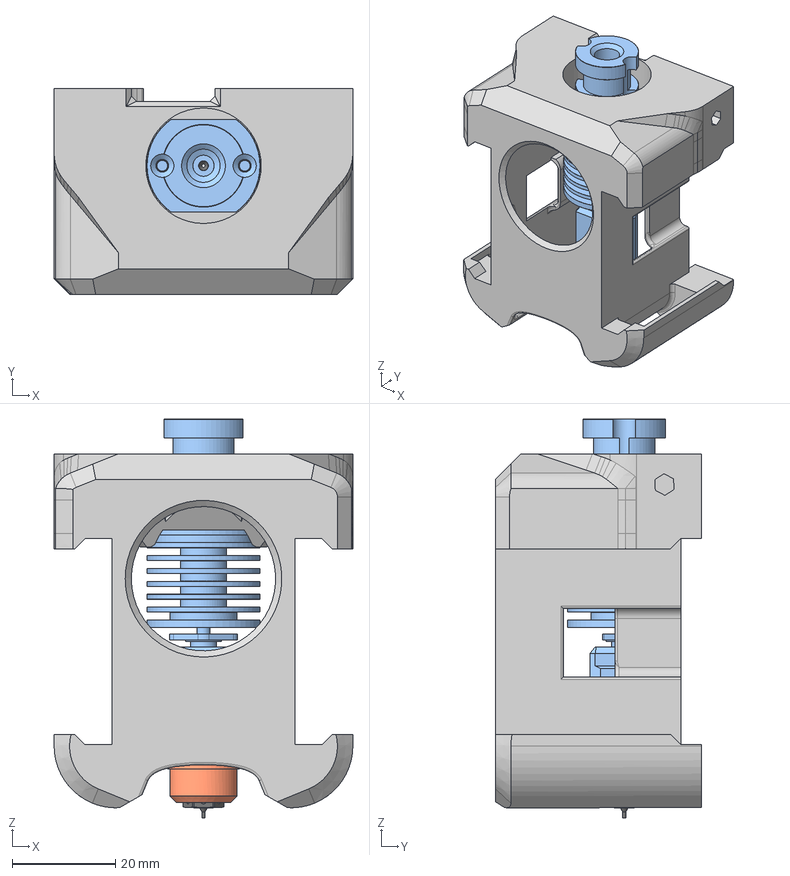
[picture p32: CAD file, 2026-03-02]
Usermods/3010 Mod fitted for Tz v6 2.0 with MZE/Burninator Tz V6 with MZE and 3010 fan.step
58.0 x 40.0 x 77.5 mm

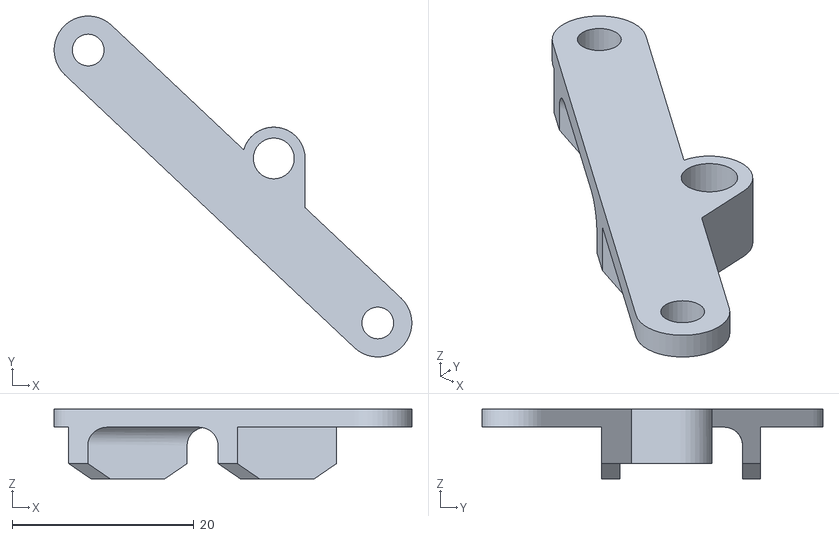
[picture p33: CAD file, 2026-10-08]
Usermods/mellow-fly-fluxheat+aspl_adaptation/fly-aspl_adapter_v2.stl
39.4 x 37.5 x 7.70

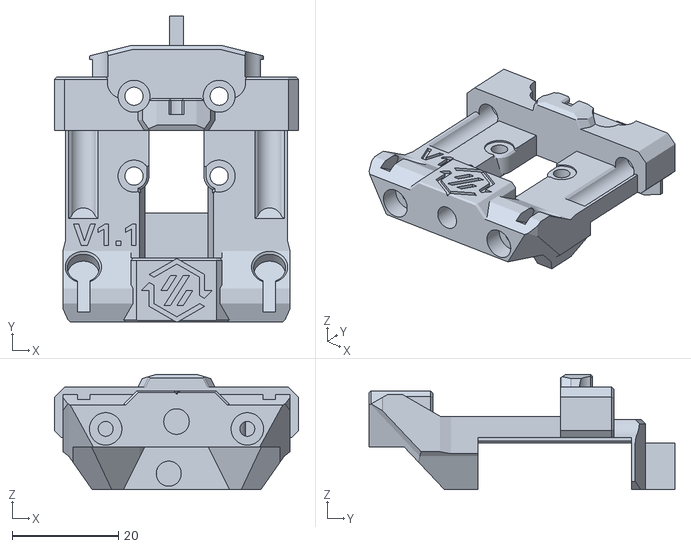
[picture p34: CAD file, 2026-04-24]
Usermods/MGN9H_shuttle_10mm_belts/MGN9H_shuttle_10mm.stl
45.9 x 57.5 x 21.7

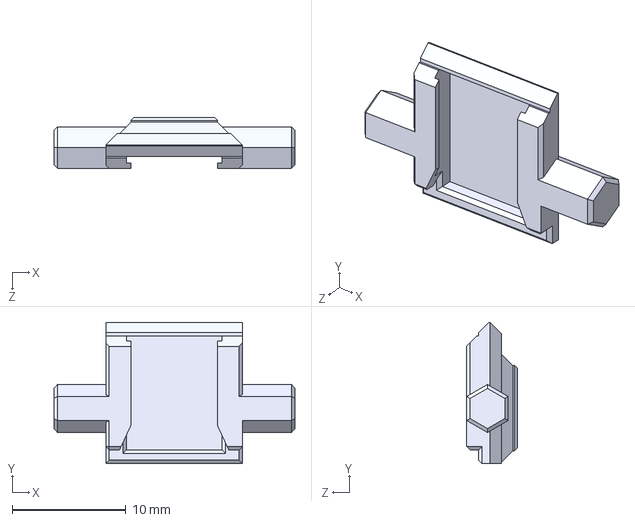
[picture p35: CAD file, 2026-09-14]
Usermods/Silicon wiper add on to dock/Wiper Holder rev5.STEP
21.2 x 12.4 x 4.45 mm

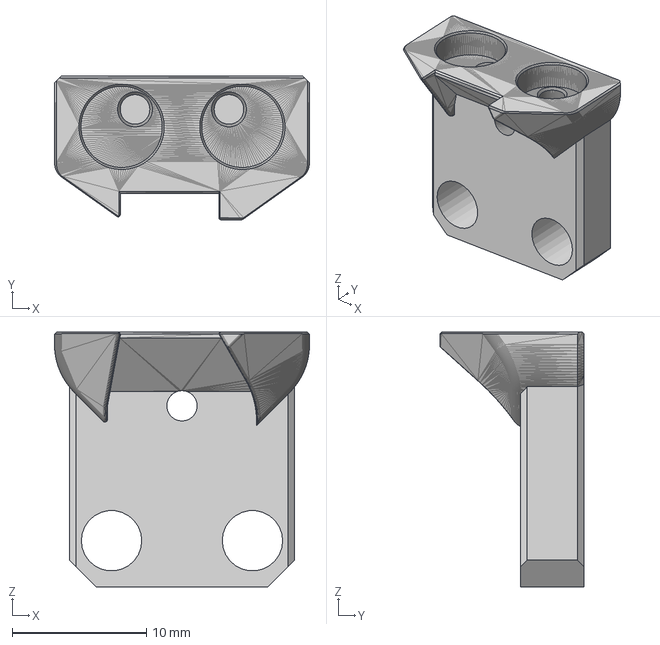
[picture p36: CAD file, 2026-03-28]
Usermods/zeroclick klicky mount/zeroclick_klicky_mount.step
19.0 x 10.7 x 19.0 mm

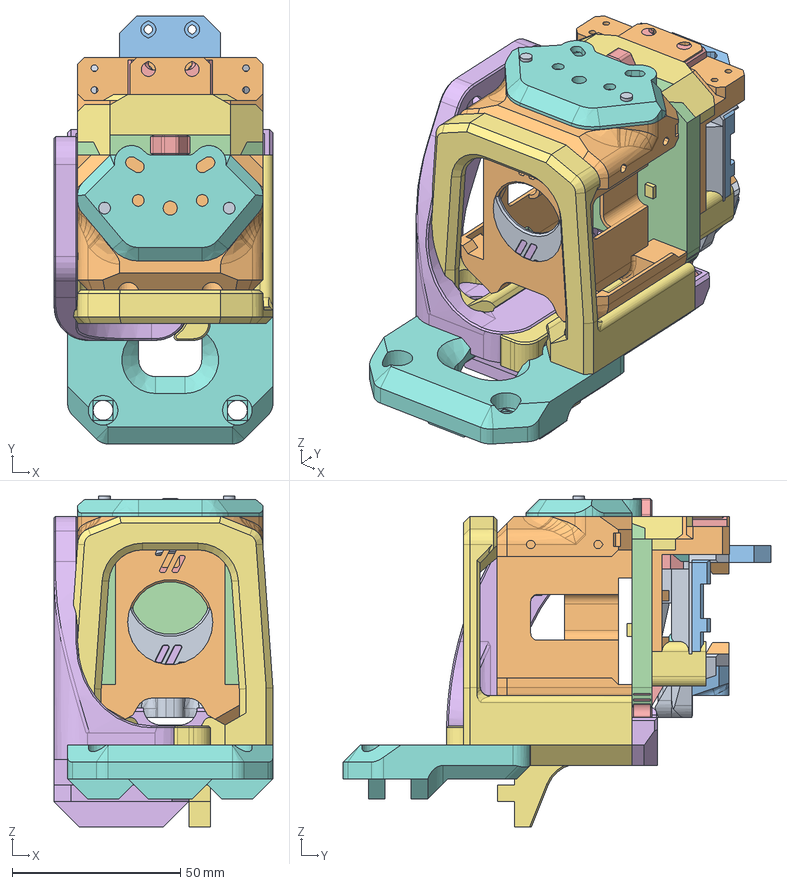
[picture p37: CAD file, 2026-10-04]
v3.0/CAD/Burninator_v3.0.step
65.0 x 127.1 x 98.3 mm

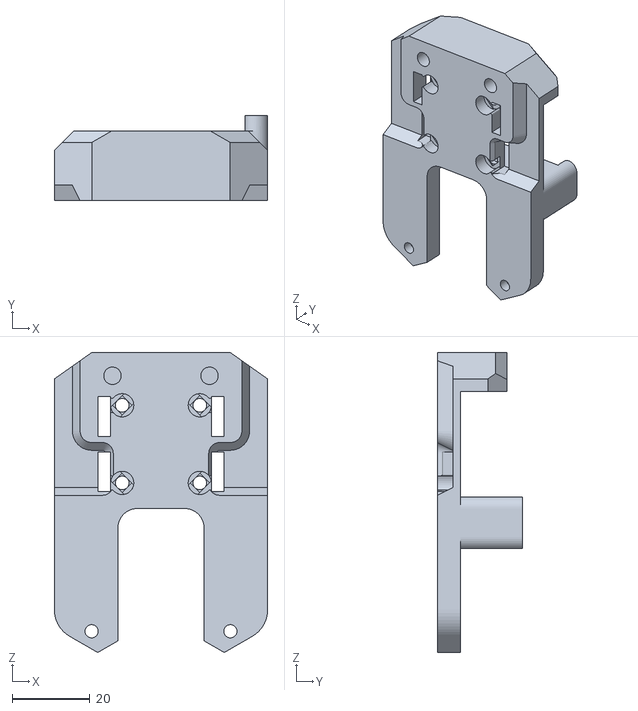
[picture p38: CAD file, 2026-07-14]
v3.0/STL/Backplates/MGN12H/MGN12H_carriage_CHC-XL.stl
55.0 x 22.0 x 77.3

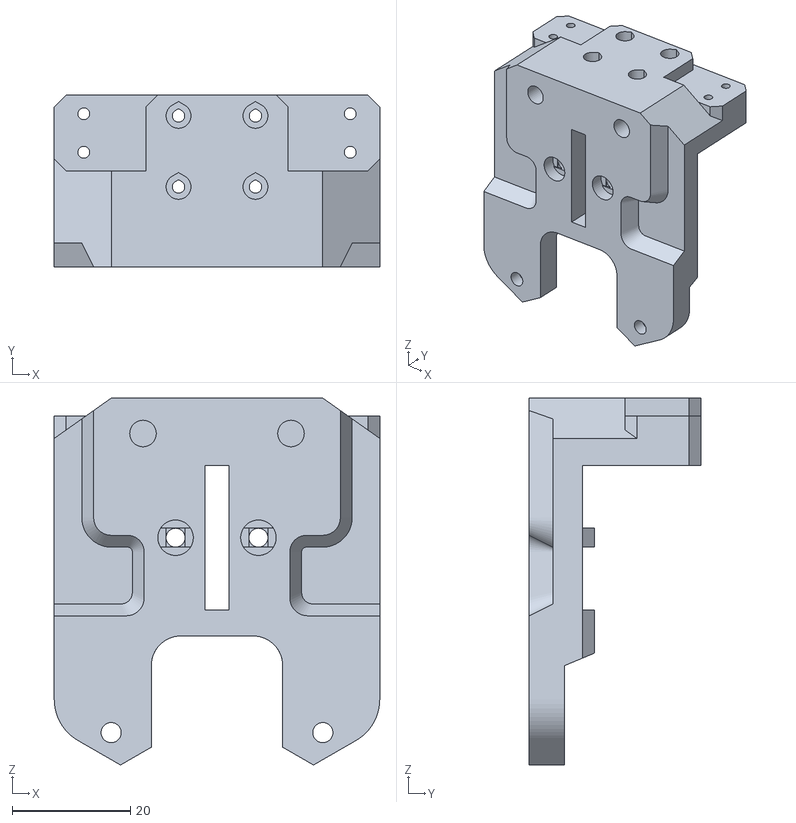
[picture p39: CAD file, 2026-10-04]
v3.0/STL/Backplates/MGN7H/MGN7H_carriage_SF+UHF.stl
55.0 x 29.0 x 62.0

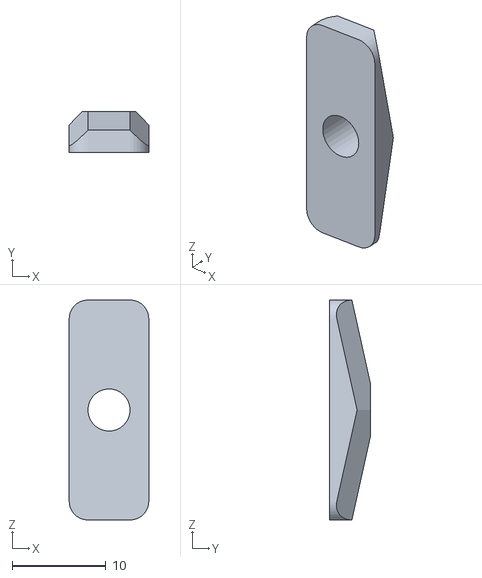
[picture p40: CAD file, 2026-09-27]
v3.0/STL/Backplates/MGN7H_belt_clamp_[2x].stl
8.50 x 4.40 x 23.5

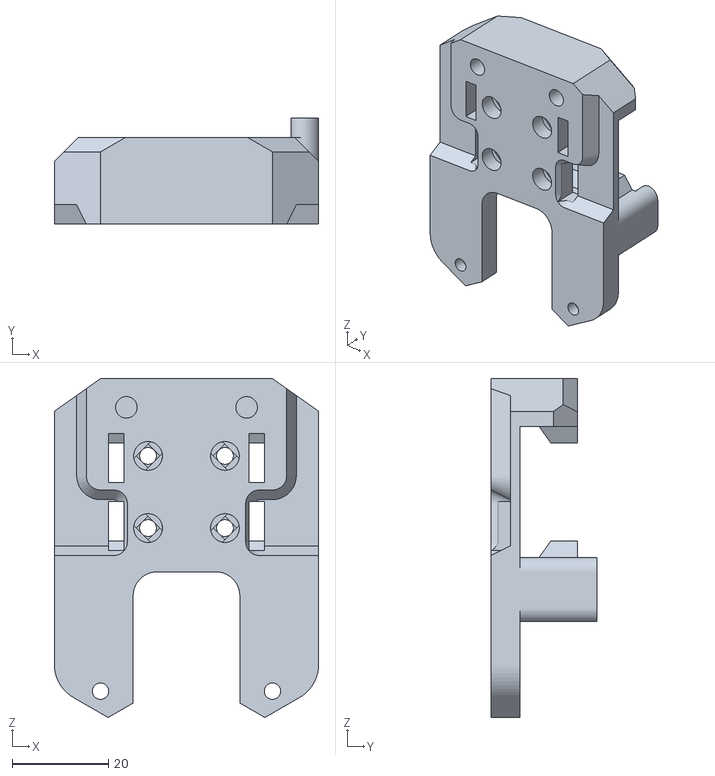
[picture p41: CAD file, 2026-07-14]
v3.0/STL/Backplates/MGN9H/MGN9H_carriage_Rapido_UHF.stl
55.0 x 22.0 x 70.5

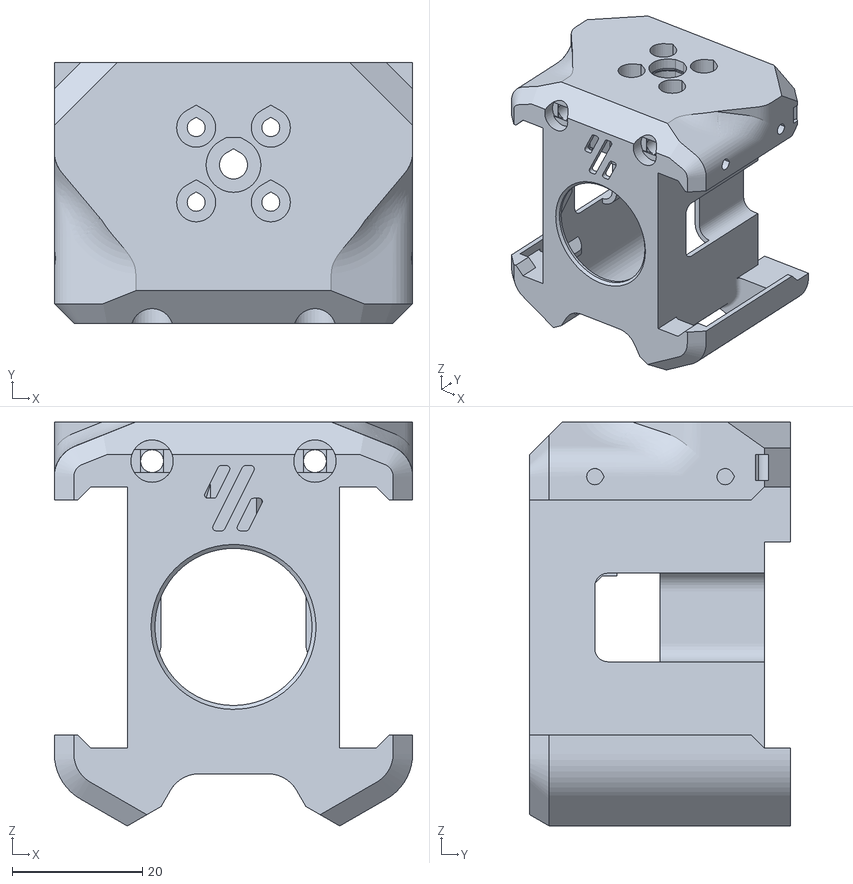
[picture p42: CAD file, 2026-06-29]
v3.0/STL/Cowls/ECAS/SF-cowl_ECAS.stl
55.0 x 40.0 x 62.0

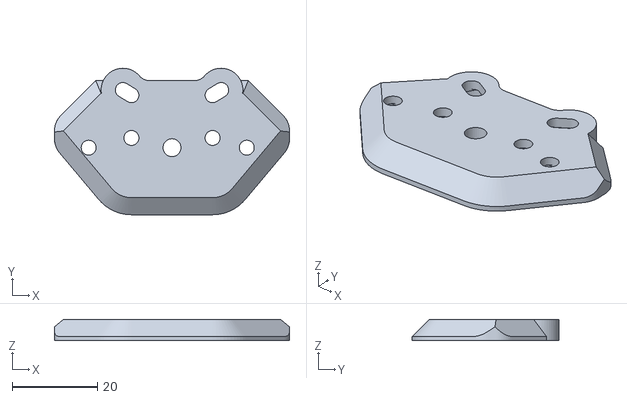
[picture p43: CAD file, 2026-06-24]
v3.0/STL/Cowls/LGX_adapter/lgx_adapter_Orbiter.stl
55.0 x 34.3 x 5.00

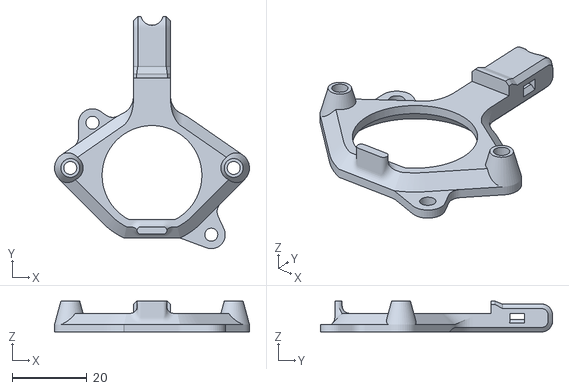
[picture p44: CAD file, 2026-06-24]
v3.0/STL/EBB36gen2_G2WW_Mount.stl
52.3 x 62.3 x 8.30

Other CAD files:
CAD/v1/Burninator_v1.step
v3.0/STL/Cowls/Orbiter/SF-cowl_Orbiter.stl
v3.0/STL/Cowls/Sherpa_Micro/SF-cowl_Sherpa_Micro.stl
v3.0/STL/Cowls/Sherpa_Mini/SF-cowl_Sherpa_Mini.stl
CAD/EBB36_Mount.step
CAD/Knob.step
STL/v1/Dock.stl
STL/v1/Dock_Cosmetic.stl
STL/v1/DraftShift_Dock_Adapter.stl
STL/v1/MGN12H_Carriage.stl
STL/v1/MGN12H_Carriage_Belt_Clamp.stl
STL/v1/MGN7H_Carriage.stl
STL/v1/MGN7H_Carriage_Belt_Clamp.stl
STL/v1/SF_parts/Cowl_SF_Cosmetic.stl
STL/v1/SF_parts/Cowl_SF_NextG_Orbiter.stl
STL/v1/SF_parts/Cowl_SF_NextG_Sherpa_Micro.stl
STL/v1/SF_parts/Cowl_SF_NextG_Sherpa_Mini.stl
STL/v1/SF_parts/LED_SF_Carrier - Kopie.stl
STL/v1/SF_parts/LED_SF_TopCarrier.stl
STL/v1/Screw_Spacer_3mm.stl
STL/v1/StealthChanger_Backplate.stl
STL/v1/UHF_parts/Cowl_Cosmetic.stl
STL/v1/UHF_parts/Cowl_NextG_Bowden_ECAS.stl
STL/v1/UHF_parts/Cowl_NextG_Orbiter.stl
STL/v1/UHF_parts/Cowl_NextG_Sherpa_Micro.stl
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

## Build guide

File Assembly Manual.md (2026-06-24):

# Assembly Manual

- Start by installing the heat inserts: two in the bottom rear, two on top of the cowl, two at the top of either the StealthChanger backplate or the MGN12H / MGN7H / MGN9H klicky carriage plus two more on the backside on beacon/cartographer carriage, two in the back of the EBB mount, one in the bottom of the dock, two in the back of the dock and two M5 inserts in the dock adapter.

<p>
 


 
 
 
 
</p>

- Insert the 2510 fan from the back and slide it upward, wedging it into place. The two small nubs should fit into the bottom holes of the fan, securing it further. This works the same way as on the Dragonburner.
- Insert the LED diffuser into the Voron logo cutout.



- Continue with soldering the LEDs. You'll need six pieces of 20mm wire and three pieces of 170mm wire.
- Solder the first three short wires to the OUT pads of the first LED.
- Solder the second LED, facing the opposite direction of the first.
- Solder the last three short wires to the second LED, facing the same direction as the first set.
- Solder the third LED so that it faces the same direction as the first LED and opposite the second.
- Solder the 170mm wire to the IN pads and crimp on the connector.  
  **Note:** Make sure the wires are soldered in the correct orientation as shown in the picture.
  
<p>
   
   
  
 
</p>

- Insert the second LED into the LED carrier first, then the remaining two, it’s easier that way.
- Insert the LED carrier from the back, placing the bottom edge into the cowl ledge. Tilt it, then press it firmly into place. Ensure the diffuser is seated in the front groove of the LED carrier.

<p>
   
   
</p>

- For the 4010 fans: remove the front cover and glue in A4T’s Backflow Inhibitor (optional but recommended).  
  After the glue has dried, put the cover pack on.
- One of the fans needs its wires bent toward the back. You may also resolder the wires.
- Slide the fans into the sides of the cowl, same as on the Dragonburner.

<p>
   
   
</p>

- Install the hotend. In my case, a Dropeffect NextG Fiber UHF is used. Ensure it's rotated correctly so the cables point toward the back corner.
- Route the thermistor wire with the cable sleeve to the opposite side, as it will not fit through the cowl and backplate cutouts. Route the heater wires on the other side, bending them so they will fit cleanly.



- Place the backplate, wiggle the cables into position, and ensure the metal hose sits inside the backplate groove underneath the center hole. Screw it down.
- Install either M3x40 SHCS screws with a 3 mm spacer, or M3x35 SHCS screws without the spacer and place a 6×3 mm magnet on top.
- Route cables into the grooves and secure them with zip-ties.
- If using the StealthChanger backplate, install the OptoTap PCB.
- If using Beacon/Cartographer carriage, now install the probe.

<p>
   
   
</p>

- Install a 22 mm PTFE tube and mount your extruder. In this example, the Galileo 2 WristWatch is used, followed by the toolhead PCB.
- In this setup, the EBB36_G2WW_Mount is required due to interference from the OptoTap.
- The toolhead is now complete.



---

# Cowl SF Assembly

- Assembling the SF cowl is only a little bit different from the UHF cowl.
- For soldering the LEDs, you need wires in the following lengths: 3 × 47 mm, 3 × 30 mm, and 3 × 170 mm.
- Start with the last LED and solder the 47 mm wires to the IN.
- Now solder the second LED, and then the first LED, using the 30 mm wires.
- Finally, solder the 170 mm wires and crimp on the connector.  
  **Note:** Make sure the wires are soldered in the correct orientation as shown in the picture.
- After that, place them into the LED carrier.

<p>


</p>

- Moving on to the cowl: first insert the LED diffuser and the top LED carrier. The cable should exit sideways into the cable channel.  
**Note:** Inside the cable channel are two little support ribs, as printing support. Just cut them away, 



- Then tuck the cable into the corner and run it down along the wall. Push the larger LED carrier aside and insert the 2510 fan.
- After that, push the larger LED carrier into place.  
  **Note:** Due to the tight space, routing the cable and seating everything can be a bit tricky. The better the soldering job and the thinner the wires, the easier it gets.



---

# Dock Assembly

- Take a 21 mm PTFE tube for the wiper and press it into the back holder.
- Press the magnets into the top.
- Screw on the back.
- Insert the 29 mm spring steel blocker into the rear slit and secure it with an M3x5 screw.
- Mount the dock onto the crossbar, optionally using the adapter.
- Dock the toolhead adjust the height of the back and the depth of the spring steel blocker

<p>
 
 
   
  </p>

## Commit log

2025-11-17 create CAD folder
2025-11-17 create STL folder
2025-11-17 edit readme
    Added a description and credits for the Burninator toolhead.
2025-11-18 edit readme
    Updated the description of the MGN12H carriage to include 'with x-endstop and klicky mount'.
2025-11-18 Update readme with CAD file usage instructionsedit readme
    Added usage instructions and notes for CAD .step file.
2025-11-18 Add header to STL readme file
2025-11-18 Update and rename CAD/UHF/Burninator.step to CAD/Burninator.step
    [Burninator.step]
2025-11-21 Fix HTML tags in STL readme for assembly manual
    Updated HTML tags in the assembly manual for better formatting.
2025-11-23 edited README
    Removed unnecessary wording from the README regarding CAD files.
2025-11-23 moved SF and UHF parts into separate folders
    [Cowl_Cosmetic.stl, Cowl_NextG_Bowden_ECAS.stl, Cowl_NextG_Orbiter.stl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]
2025-11-23 renamed file
    [LED_SF_TopCarrier.stl]
2025-11-23 deleted missplaced file
    [Cowl_SF_NextG_Sherpa_Micro - Kopie.stl]
2025-11-23 edit text
    Added support for the Voron V0 hotend.
2025-11-25 Enhance readme with cosmetic alignment details
    Added alignment notes for cosmetic parts in printing instructions.
2025-11-29 reorganize files for adding v2
    [Cowl_Cosmetic.stl, Cowl_NextG_Bowden_ECAS.stl, Cowl_NextG_Orbiter.stl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]
2025-11-30 Update README
    Added notes on hotend dimensions for compatibility.
2025-12-02 Update assembly instructions for heat inserts
2025-12-06 Add disclaimer regarding Z-joint assembly issues
    Added a disclaimer about potential issues with Z-joints and toolhead height.
2026-03-02 Moved file from pullrequest into Usermods; Edited readmes
    [Burninator Tz V6 with MZE and 3010 fan.step]
2026-03-13 adding usermods
    [CHC-XL_SC-Backplate.3mf, CHC-XL_SC-Dock.3mf, CHC-XL_SC.step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]
2026-03-14 Update feature description for clarity
    Clarified wording regarding the UHF hotend example.
2026-03-17 Add readme for MGN12H invertable belt fixture
    This readme provides details about a test piece for mounting 9mm belts to the MGN12H carriage using an invertable fixture.
2026-03-20 Add Usermod
    [CHC-XL_MZE.step, CHC-XL_MZE_ECAS.stl, CHC-XL_MZE_orbiter.stl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]
2026-06-10 clone repo; rearrange files and folders; delete and add files; prepair for v3.0
    [A4T Backflow Inhibitor [x2](1).stl, A4T Backflow Inhibitor [x2].stl, A4T Backflow Inhibitor install spacer tool.stl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]
2026-06-11 updated v3.0 files
    [Burninator_v3.0.f3d, Burninator_v3.0.step, Burninator_v3.f3d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]
2026-06-19 updating v3.0 files
    [Burninator_v3.0.f3d, Burninator_v3.0.step, MGN7H_carriage_CHC-XL+MZE.stl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]
2026-06-21 Rename LED__SF_carrier.jpg to LED_SF_carrier.jpg
    fixed file name typo
2026-06-21 Update Assembly Manual.md
2026-06-21 update v3.0 files
    [CHC-XL+MZE-cowl_ECAS.stl, CHC-XL+MZE-cowl_Orbiter.stl, CHC-XL+MZE-cowl_Sherpa_Micro.stl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]
2026-06-24 add EBBgen2 mounts
    [EBB36_Mount.step, EBB36gen1_G2SA_Mount.stl, EBB36gen1_G2WW_Mount.stl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]
2026-06-28 Updated SC files
    [Burninator_v3.0.f3d, Burninator_v3.0.step, SC_backplate_CHC-XL+MZE.stl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]
2026-06-28 updated LED files
    [SF_carrier.stl, UHF_carrier.stl]
2026-06-29 updated SF_cowl andd MM_Backplates
    [MM_backplate_CHC-XL+MZE.stl, MM_backplate_CHC-XL.stl, MM_backplate_Rapido_UHF.stl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]
2026-06-29 updated CAD files
    [Burninator_v3.0.f3d, Burninator_v3.0.step]
2026-06-29 fixed upload mistake
    [MM_backplate_CHC-XL+MZE.stl, MM_backplate_CHC-XL.stl, MM_backplate_Rapido_UHF.stl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]
